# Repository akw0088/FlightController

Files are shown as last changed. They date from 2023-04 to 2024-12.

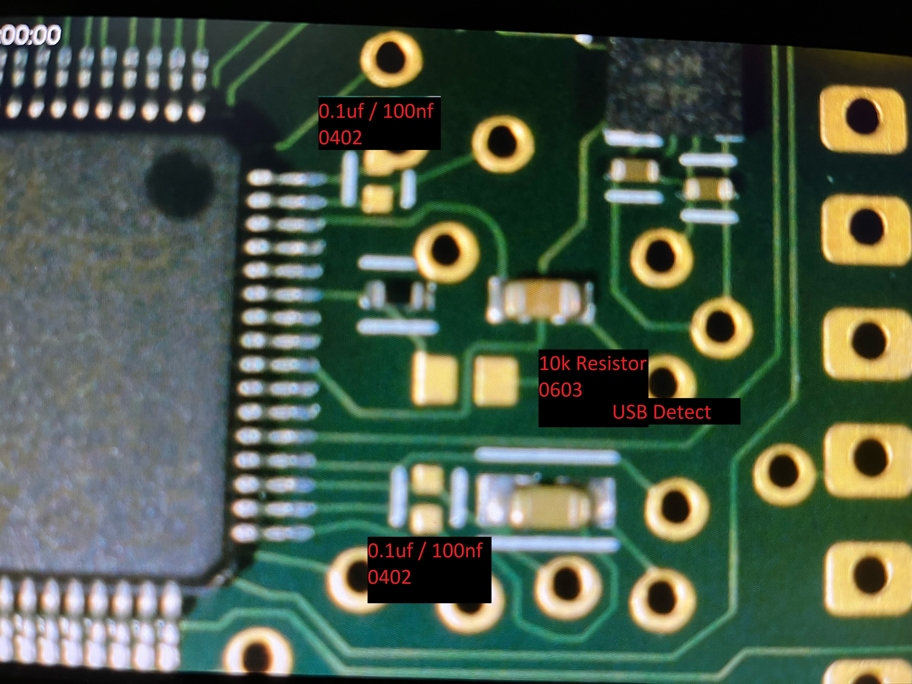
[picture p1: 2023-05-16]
boards/rev1/SMD_to_solder/image1.jpeg

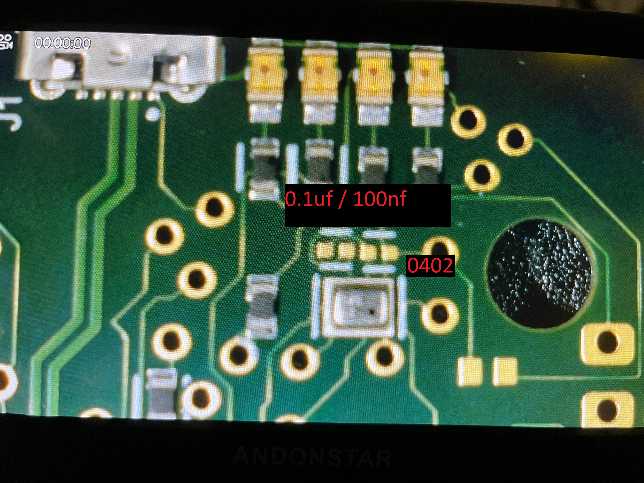
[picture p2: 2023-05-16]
boards/rev1/SMD_to_solder/image4.jpeg

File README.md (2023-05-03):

# FlightController

Figured I should design a PCB and a flight controller seemed pretty approachable compared to how complicated PC's are getting. DroneMesh designed a F4 flight controller that uses essentially three chips. The Gyro MPU6000, the processor STM32F4xx, and one diode to feed the 3.3v regulator from USB or external 5v. I would like to make a F7 flight controller and would like for it to be similar to the JBF7_V2. I am currently using Altium Designer for schematic and layout (get a free license due to my masters degreee) but I will likely make the files available in as many formats as I possibly can (KiCad, Cadence, EasyEDA, DipTrace, others?)

For the most part the schematic is the most useful, as I find this is really an exercise in picking chips and connecting nets together, layout can be automated quite a bit, but I'm sure manual part placement will occur as well as setting the 30x30 size and 4mm mounting holes.

		"Special Pins" have timers, like motor outputs, camera control, LED_STRIP, etc

For manufacturing I'll probably use PCBWay or JLCPCB

Good video/channel on PCB design:

https://www.youtube.com/watch?v=aVUqaB0IMh4

Altium specific video (cross probing two windows is awesome):

https://www.youtube.com/watch?v=PMEpQZ90f34

Links to drone meshes stuff:

https://oshwlab.com/mesh.drone/mesh-fc-v1-backup

https://www.pcbway.com/project/member/?bmbno=82F43017-E23A-4A

https://www.youtube.com/c/DroneMesh

Drone mesh PCB with OSD chip (not sure he ever got it working):

https://easyeda.com/modules/DroneMesh-OpenFC-Schematic_02d7d85512334af9a66e7b7c09a951f3

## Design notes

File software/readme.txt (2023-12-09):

Above is mostly auto generated from STM32CubeIDE

	Bootloader boot works
	Software runs when programming from bootloader
	Clocking issue resolved USB in non-bootloader mode
	(8mhz external clock HSE, was set to 27mhz originally as that was what was originally in the BOM, but what was built on the PCB was actually 8mhz, which is good, because the max clock I see on the CubeIDE is 26mhz)
	USB currently comes up as STMicroelectronics Virtual COM Port (COM3)
	Need to add some software to support updating when in non-bootloader mode
	(maybe serial command to enter DFU mode?)
	Idea was to just use BetaFlight unmodified, but I'm assuming clocking differences are preventing the USB from coming up

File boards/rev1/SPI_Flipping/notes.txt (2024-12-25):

In the rev1 boards I got MOSI/MISO pins backwards to the Gyro and the Barometer (mainly because they renamed them SDI/SDO for political correctness)

So, to fix them I used a NF.V2 Grinding Pen to cut the traces
(probably overkill, as I could have probably just used a snap away razor knife to cut the traces, eg: https://www.youtube.com/watch?v=ozH2F3AX8BY)

I suppose the grinding pen can get middle layer traces also if you are delicate

Anyway, looking at the small size of these traces I think soldering to them would be pretty difficult, so I think between copper tape and conductive ink pen I can connect them more easily. Although the pen is kind of pricey at $60 and has a short shelf life of 18 months. (Bought this one: CW2200MTP)

In summary: I ordered five rev1 boards, two have SMD component soldered up and work. (Not all components were pick and placed) Board one I shorted the voltage regulator, but can still be used for testing the Analog video OCD chip I believe. The next two boards had the SMD components soldered and work, and that leaves two untouched boards.

Probably would have been faster to just order more boards with the trace fixed in software and worked with JLCPCB to get all the SMD components connected from factory. But I want Rev2 to be perfect or near perfect so the more I can test on rev1 the better.

(That said I made rev1 in about a week while taking time off work when I had a wisdom tooth removed and probably should have reviewed the schematic more intensely prior to getting it made)

12/24/2024

Added solder pen to the board for the SPI flip on the gyro only for now. Passes basic conductivity checks with a multimeter. Got really close to the vias but I lucked out, almost seems like a slight edge there preventing accidental bridging which is nice

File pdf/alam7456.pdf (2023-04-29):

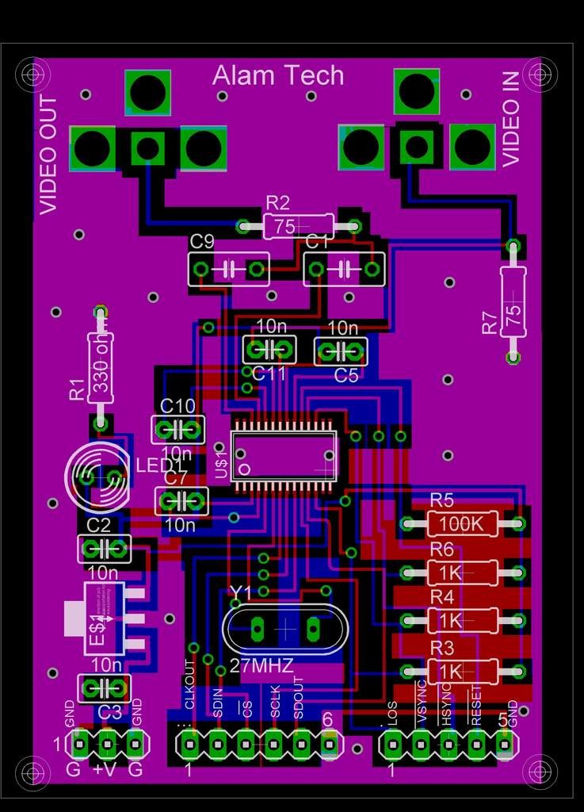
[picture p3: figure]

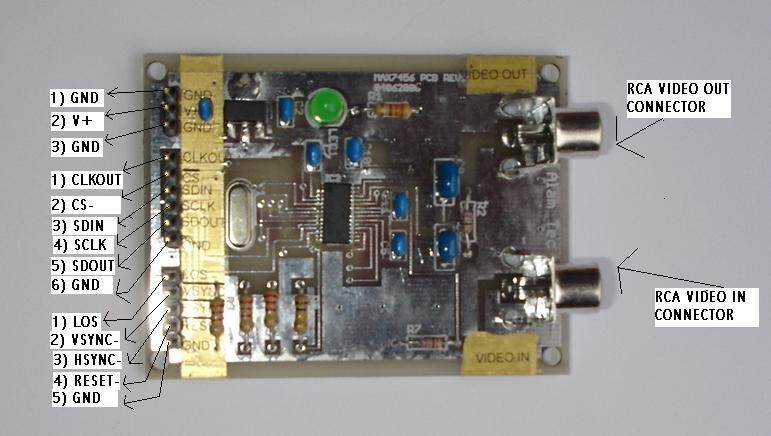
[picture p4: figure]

MAX7456 DEV BOARD WITH ALL SIGNALS INFO

### MAX7456 ON SCREEN DISPLAY DEVLOPMENT BOARD

General Description:
The MAX7456 Development Board is a fully assembled and tested Printed-Circuit Board (PCB) that supports SPI interface to MAX7456 signal-channel monochrome on-screen display (OSD) with integrated video driver.

The MAX7456 is single channel monochrome on-screen display(OSD) generator lowers the system cost by eliminating the need for an external video driver, sync separator, video switch and EEPROM. The MAX7456 serves all market with 256 user programmable characters in NTSC and PAL Standards.

The MAX7456 can easily display information such as
1. Company logo.
2. Custom graphics.
3. Time.
4. Date.
5. Arbitrary character size.

The MAX7456 is preloaded with 256 characters and pictograph and can be reprogrammed in-circuit using SPI port.

The MAX7456 is available in a 28 pin TSSOP package and is fully specified over the extended (-40 degree C to +85 degree C) temperature range.

The power LED shows the +5V on board.
Total current MAX7456 board consumes is around 100 ma, power consumption is around 0.5W.

Application:
Security Switching Systems.
Security Cameras.
Industrial Application.
In-Cabin Entertainment.
Consumer Electronics.

Recommended Equipment:
VCC accepts 7-12 Volt 250ma power supply. NTSC or PAL signal source.
NTSC or PAL video monitor.
Video Cable (RCA cable not included).

Do not turn on the power until all connections are made.

Features:
256 User-Defined Character or Pictograph in integrated EEPROM. 12X18 Pixel Character Size.
Blinking, Inverse and Background Control Character Attribute. Selectable Brightness by Row.
Display up to 16 Row and 30 Characters.
Sag Compensation on Video-Driver Outputs.
LOS, VSYNC(active low), HSYNC(active low) and clock output. Integral Sync Generation.
NTSC and PAL Compatible.
SPI-Compatible Serial Interface.
Delivered With Preprogrammed Character Set.

MAX7456 Dev Board Signals:
1. LOS: LOS goes high when 32 consecutive valid sync pulses are missing. Connect to 1k or 2.2 k pull up resistor to DVDD or another positive supply voltage suitable for the receiving device. If user want different pull up he can cut the pull up resistor and user external ones.
2. VSYNC: Vertical Sync Output (Open Drain, active low). VSYNC goes low following the video input vertical sync internal. VSYNC is either recovered from VIN or internally generated when internal sync mode used. Connect to 1k or 2.2 k pull up resistor to DVDD or another positive supply voltage suitable for the receiving device. If user want different pull up he can cut the pull up resistor and user external ones.
3. HSYNC: Horizontal Sync Output (Open Drain, active low). HSYNC goes low following the video input horizontal sync interval.
4. RESET: System Reset Input. The minimum RESET Pulse width is 50 msec. All SPI register are reset to their default values after 100 usec following rising edge of RESET. The display memory is reset to its default value of 00h in all location after 20usec following the rising edge of RESET.
5. VIDEO IPUT: The MAX7456 accepts NTSC or PAL CVBS Signals at VIN. The video signal input must be AC-Coupled with a 0.1uf capacitor and internally coupled. An input coupling capacitance of 0.1uf is required to guarantee the specific line-time distortion (LTD) and video clamp setting time.
6. Sync Separator: The sync separator detects the composite sync pulses on the Video Input and extracts the timing information to generate HSYNC and VSYNC. LOS goes high if no sync signal is detected at VIN for 32 consecutive lines and goes low if 32 consecutive horizontal sync signals are detected.
7. Serial Interface: The SPI compatible Serial Interface programs the operating mode and OSD data Read capability permits Write verification and reading the status (STAT), Display Memory Data Out (DMDO) and Character Memory Data Out(CMDO) registers.
8. Video-Driver Output: The MAX7456 includes a Video-driver output with a gain of 2. The driver has a maximum of 2.4Vp-p output swing and a 6MHZ large signal bandwidth. The driver is capable of driving two 150ohms standard video loads.

For MAX7456 data sheet, please check these links, you will find sample code along with other useful information.

http://www.maxim-ic.com/
http://www.rcgroups.com/forums/showthread.php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

Here is the video at youtube.
http://www.youtube.com/watch?v=RTPLH7UWspw

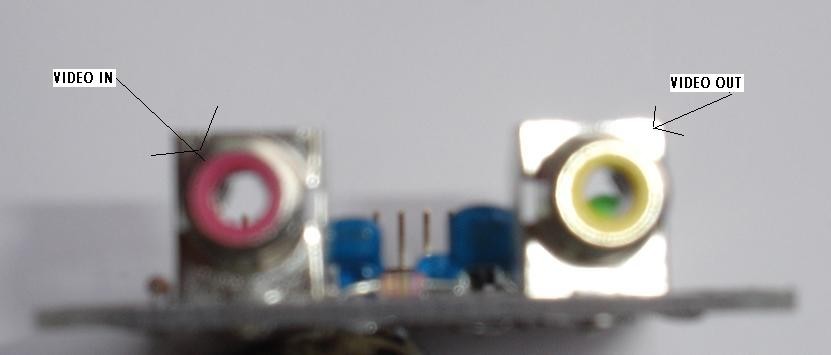
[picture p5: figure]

MAX7456 DEV BOARD VIDEO IN-OUT RCA CONNECTOR

MAX7456 DEV BOARD COMPLETE LAYOUT

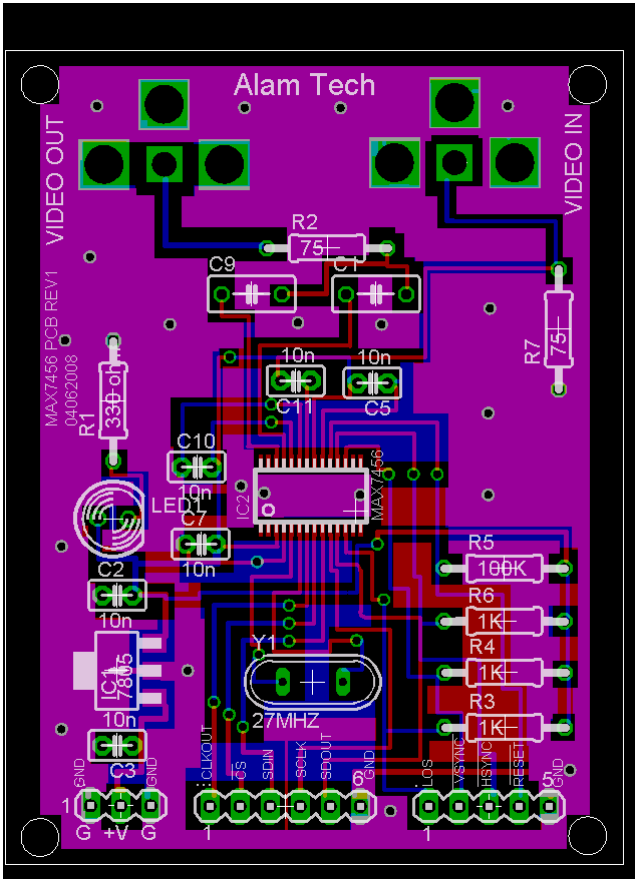
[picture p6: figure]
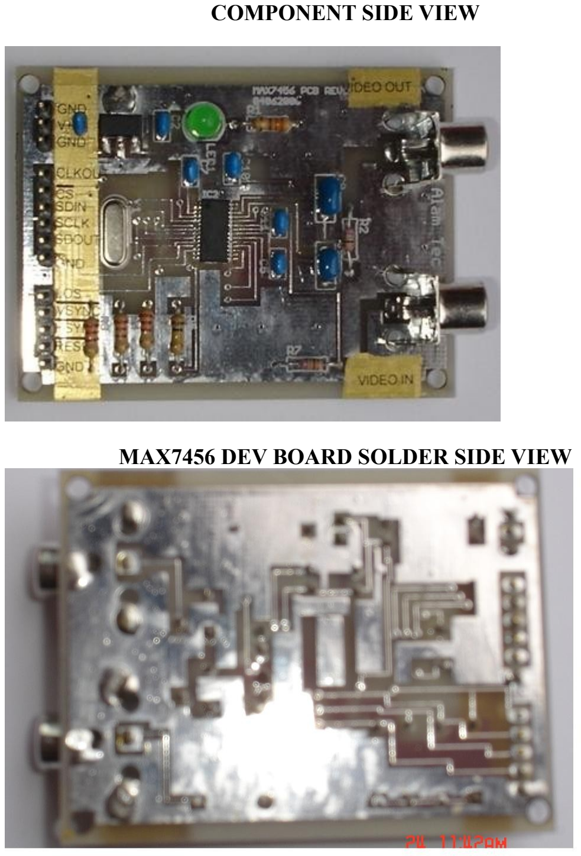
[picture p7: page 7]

COMPONENT SIDE VIEW

MAX7456 DEV BOARD SOLDER SIDE VIEW

Here is the function, I just wrote it for testing your sequence.

void show_misc_data_display (void)
{
/* ENABLE VIDEO OUTPUT */
max7456_add_reg = MAX7456_VIDEO_0_REG_ADD; max7456_data_reg = ENABLE_DISPLAY_OSD_IMAGE; spi_enable_cs_new();
/* send 8 bit address */
spi_send_data_to_spi_port(max7456_add_reg);
/* send 8 bit data */
spi_send_data_to_spi_port(max7456_data_reg); spi_disable_cs();

/* SEND ADDRESS */
max7456_add_reg = MAX7456_DISPLAY_MEMORY_ADDRESS_HIGH; max7456_data_reg = 0x00;
spi_enable_cs_new();
/* send 8 bit address */
spi_send_data_to_spi_port(max7456_add_reg); /* send 8 bit data */
spi_send_data_to_spi_port(max7456_data_reg); spi_disable_cs();
max7456_add_reg = MAX7456_DISPLAY_MEMORY_ADDRESS_LOW; max7456_data_reg = 0xE0;
spi_enable_cs_new();
/* send 8 bit address */
spi_send_data_to_spi_port(max7456_add_reg); /* send 8 bit data */
spi_send_data_to_spi_port(max7456_data_reg); spi_disable_cs();
/* SEND DATA */
max7456_add_reg = MAX7456_DISPLAY_DATA_IN; max7456_data_reg = 0x0B;
spi_enable_cs_new();
spi_send_data_to_spi_port(max7456_add_reg); spi_send_data_to_spi_port(max7456_data_reg); spi_disable_cs();

/* SEND ADDRESS */
max7456_add_reg = MAX7456_DISPLAY_MEMORY_ADDRESS_HIGH; max7456_data_reg = 0x00;
spi_enable_cs_new();
/* send 8 bit address */
spi_send_data_to_spi_port(max7456_add_reg); /* send 8 bit data */
spi_send_data_to_spi_port(max7456_data_reg); spi_disable_cs();
max7456_add_reg = MAX7456_DISPLAY_MEMORY_ADDRESS_LOW; max7456_data_reg = 0xE1;
spi_enable_cs_new();
spi_send_data_to_spi_port(max7456_add_reg); spi_send_data_to_spi_port(max7456_data_reg);

spi_disable_cs();
/* SEND DATA */
max7456_add_reg = MAX7456_DISPLAY_DATA_IN; max7456_data_reg = 0x0C;
spi_enable_cs_new();
spi_send_data_to_spi_port(max7456_add_reg); spi_send_data_to_spi_port(max7456_data_reg); spi_disable_cs();

/* SEND ADDRESS */
max7456_add_reg = MAX7456_DISPLAY_MEMORY_ADDRESS_HIGH; max7456_data_reg = 0x00;
spi_enable_cs_new();
spi_send_data_to_spi_port(max7456_add_reg); spi_send_data_to_spi_port(max7456_data_reg); spi_disable_cs();
max7456_add_reg = MAX7456_DISPLAY_MEMORY_ADDRESS_LOW; max7456_data_reg = 0xE2;
spi_enable_cs_new();
spi_send_data_to_spi_port(max7456_add_reg); spi_send_data_to_spi_port(max7456_data_reg); spi_disable_cs();
/* SEND DATA */
max7456_add_reg = MAX7456_DISPLAY_DATA_IN; max7456_data_reg = 0x0D;
spi_enable_cs_new();
spi_send_data_to_spi_port(max7456_add_reg); spi_send_data_to_spi_port(max7456_data_reg); spi_disable_cs();
}

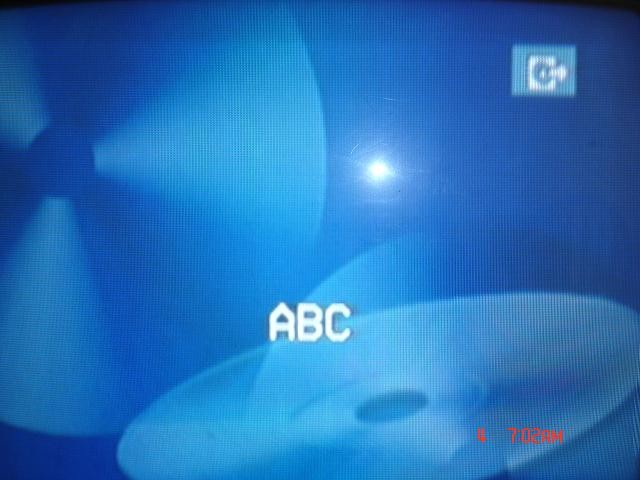
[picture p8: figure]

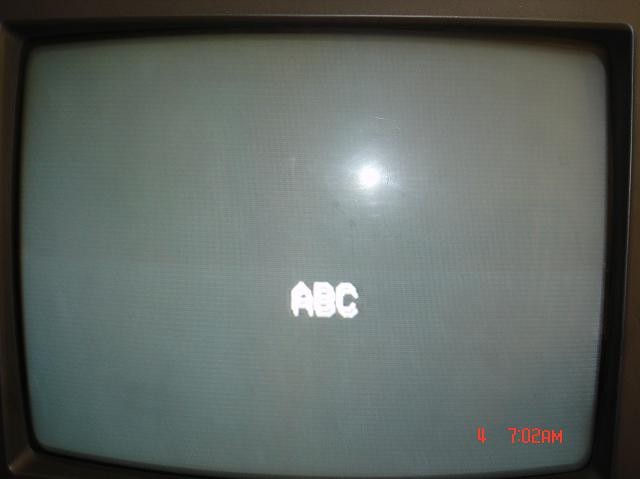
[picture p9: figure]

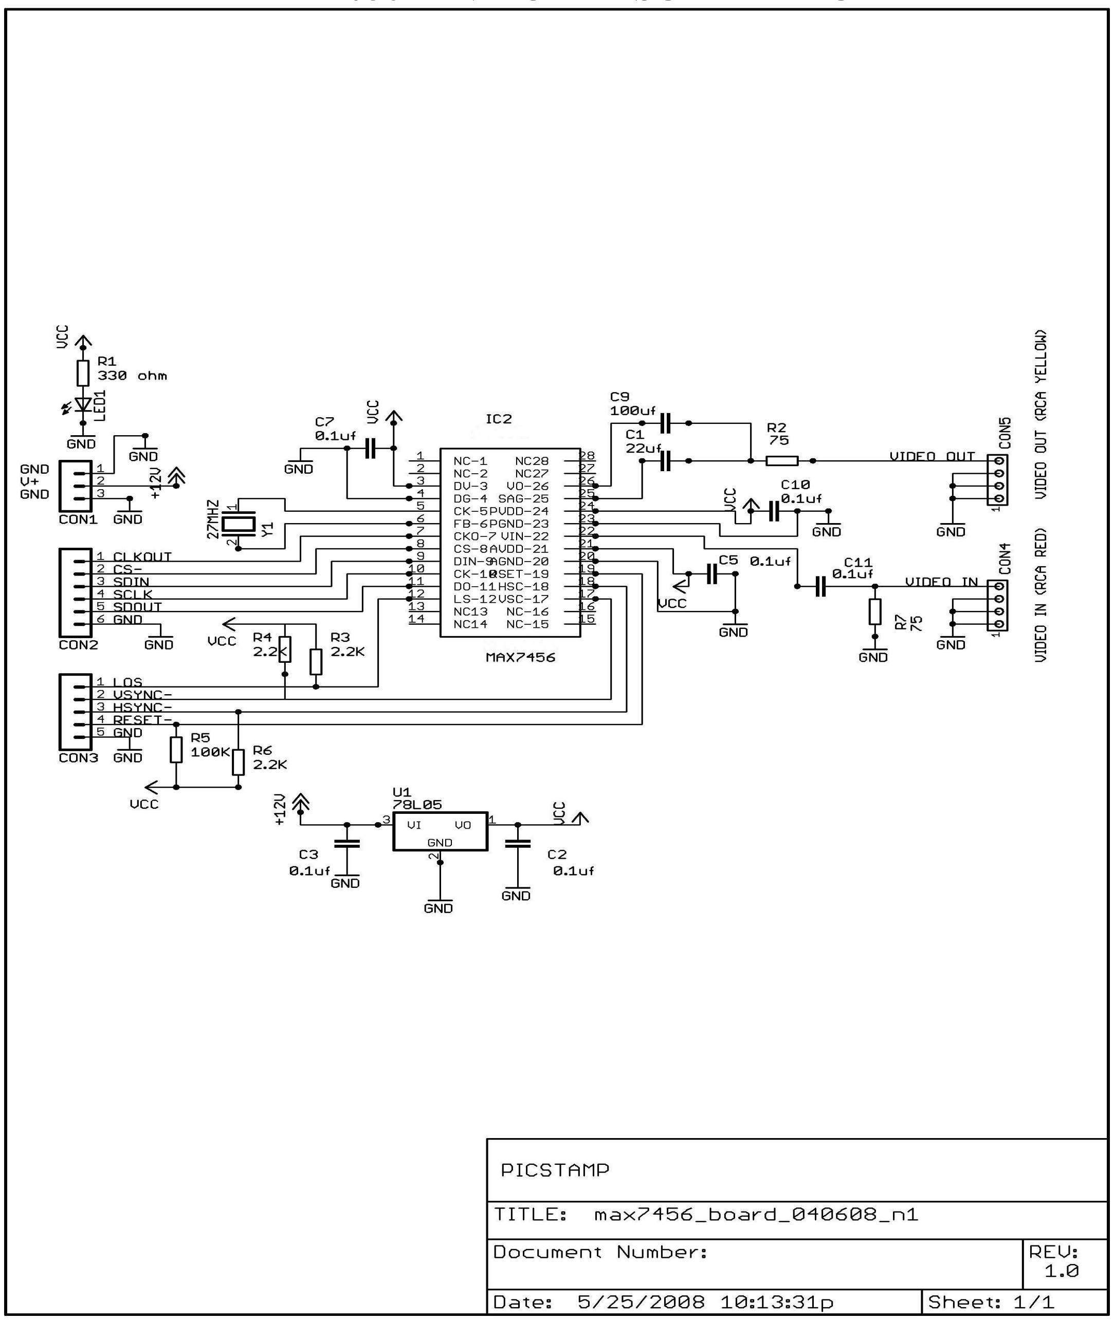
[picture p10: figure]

MAX756 DEV BOARD SCHEMATIC

MAX7456 Board Specification:
1. Board width is 2.0625 inches.
2. Board length is 2.625 inches.
3. Board weight is 0.6250 oz (20 grams).

MAX7456 Board using with +5v supply:

Please short the pin 1 with pin 3 of U1 (7805) voltage regulator.
Check the picture below, just short the pin1 and pin3, so by doing this voltage regulator can be bypass.
Please disconnect R3, R4, R5, R6 if you want to connect the LOS, RESET, VSYNC, HSYNC to 3.3 volt device, use external pull up resistors. All these signals are pull up using +5 volt.

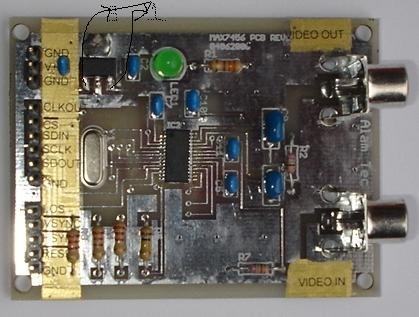
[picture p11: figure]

MAX756 DEV BOARD CONNETORS:

CON1: (MAIN POWER IN)
INTERFACE | PIN
GND | 1
VCC (+7 to +15V) | 2
GND | 3

CON2: (SPI INTERFACE)
INTERFACE | PIN
CLKOUT (MAX7456 CLK OUT) | 1
CS- (SPI) | 2
SDIN (SPI) | 3
SCLK (SPI) | 4
SDOUT (SPI) | 5
GND | 6

CON3: (MAX7456 STATUS OUT)
INTERFACE | PIN
LOS (ACTIVE HIGH) | 1
VSYNC - (ACTIVE LOW) | 2
HSYNC - (ACTIVE LOW) | 3
RESET- (ACTIVE LOW) | 4
GND | 5

CON4: (RCA VIDEO IN CONNECTOR)
INTERFACE | PIN
GND | 1
GND | 2
GND | 3
VIDEO IN (NTSC/PAL) | 4

CON5: (RCA VIDEO OUT CONNECTOR)
INTERFACE | PIN
GND | 1
GND | 2
GND | 3
VIDEO OUT (NTSC/PAL) | 4

MAX756 Dev Board Part List:

PARTS | SPECS | MECH SPEC
CON1 | 3 PIN (POWER) | 0.1 INCH SPACING
CON2 | 6 PIN (SPI) | 0.1 INCH SPACING
CON3 | 5 PIN (SIGNALS) | 0.1 INCH SPACING
CON4 | 4 PIN (VIDEO IN) | RCA CONNECTOR
CON5 | 4 PIN (VIDEIO OUT) | RCA CONNECTOR
R1 | 330 OHMS | ¼ W
LED1 | GREEN LED
Y1 | 27 MHZ
C7 | 0.1 UF | 50 V
R4 | 2.2 K | ¼ W
R3 | 2.2 K | ¼ W
R5 | 100 K | ¼ W
R6 | 2.2 K | ¼ W
U1 | 78L05 | 500 ma +5v regulator
C9 | 100 UF | 16 V
C1 | 22 UF | 16 V
R2 | 75 OHMS | ¼ W
C10 | 0.1UF | 50 V
C5 | 0.1UF | 50 V
C11 | 0.1UF | 50V
R7 | 75 OHMS
IC2 | MAX7456 | 28 PIN TSSOP
C3 | 0.1UF | 50 V
C2 | 0.1UF | 50V

For more information please contact.

Fakhre Alam
AlamTech
4985 West 7th St, #10
Reno, Nevada, 89503
U.S.A.
fakhre@rocketmail.com

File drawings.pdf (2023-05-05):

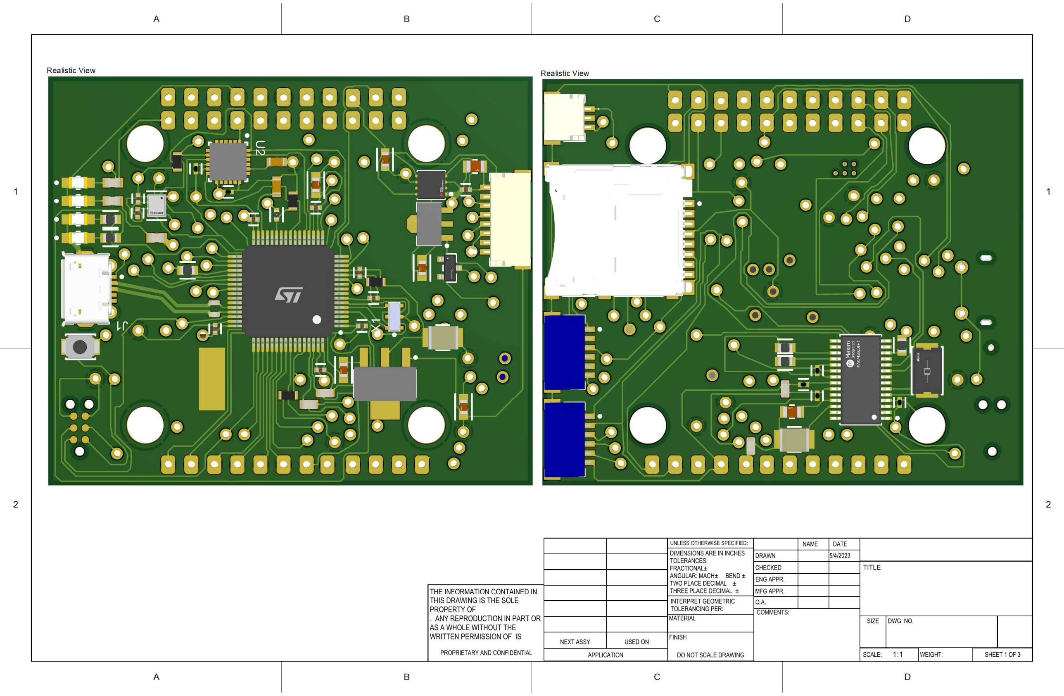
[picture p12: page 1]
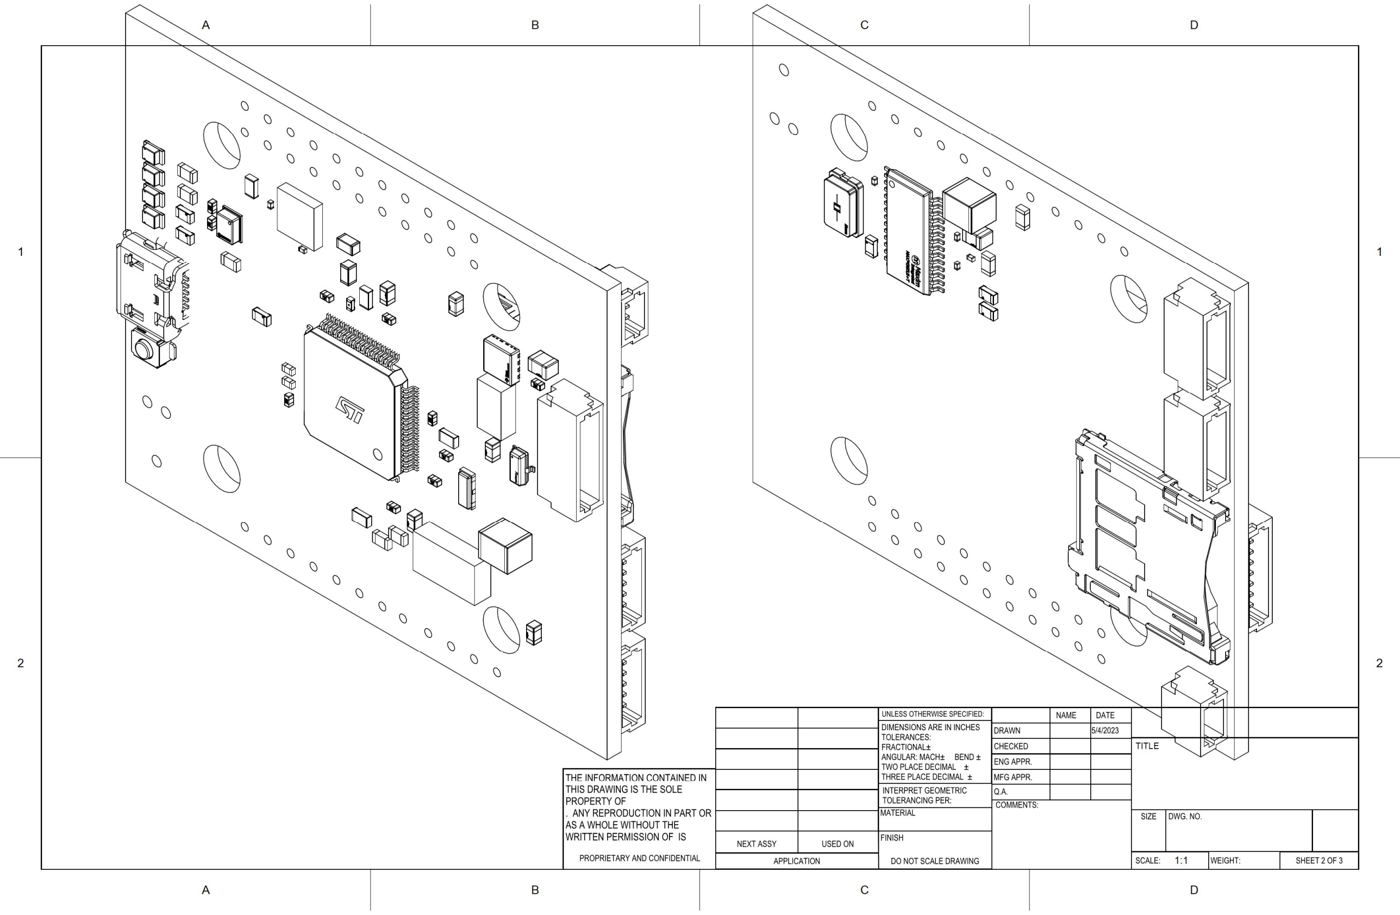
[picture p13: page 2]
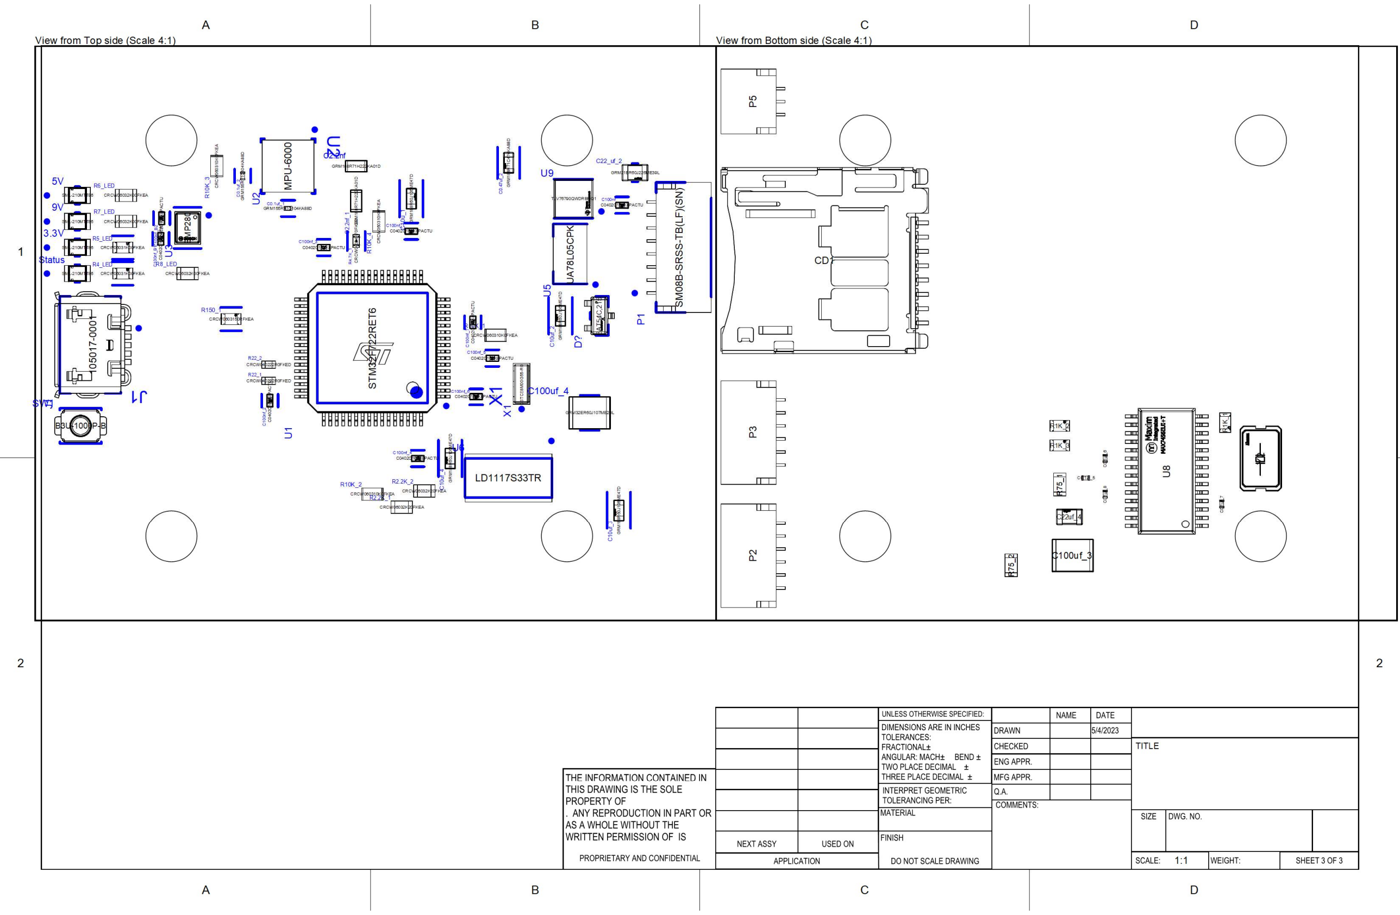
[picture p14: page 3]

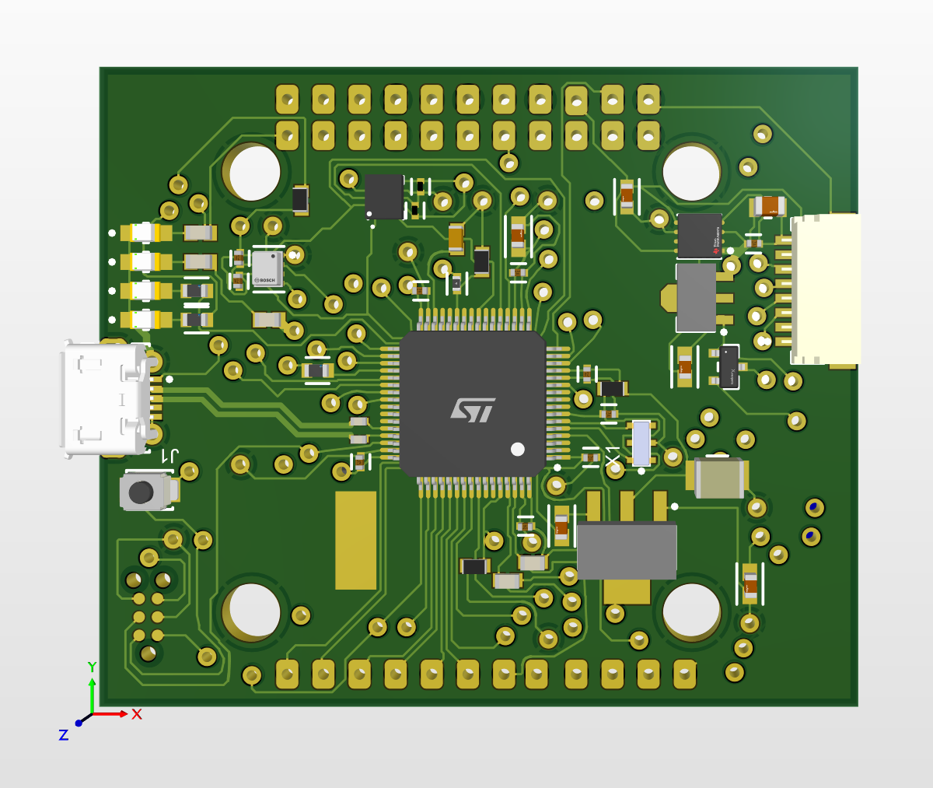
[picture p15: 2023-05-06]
top.png

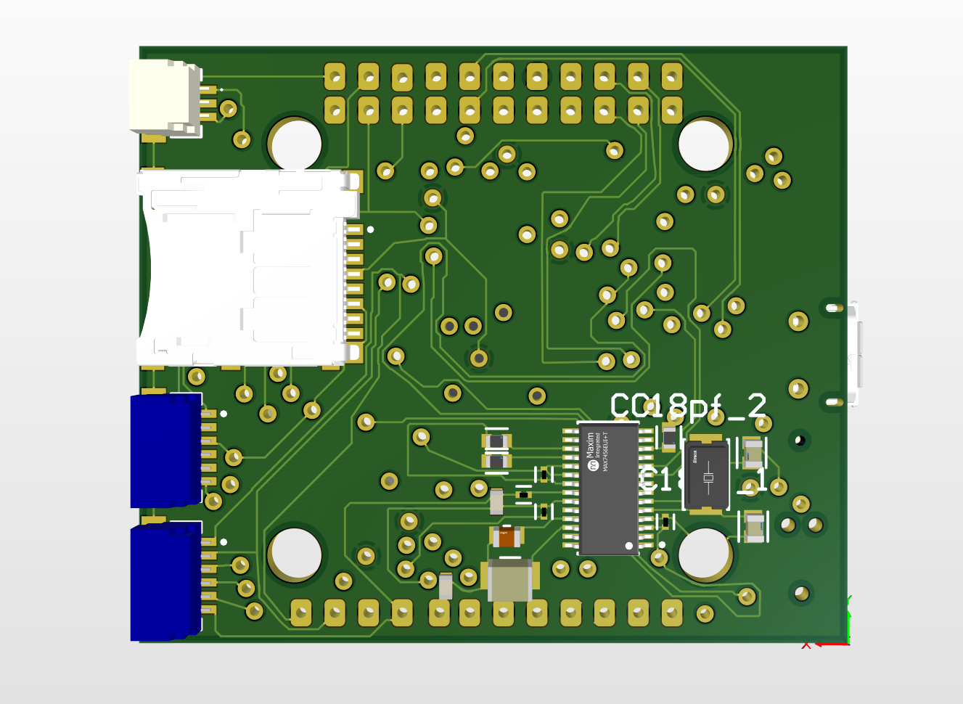
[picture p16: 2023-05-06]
bottom.png

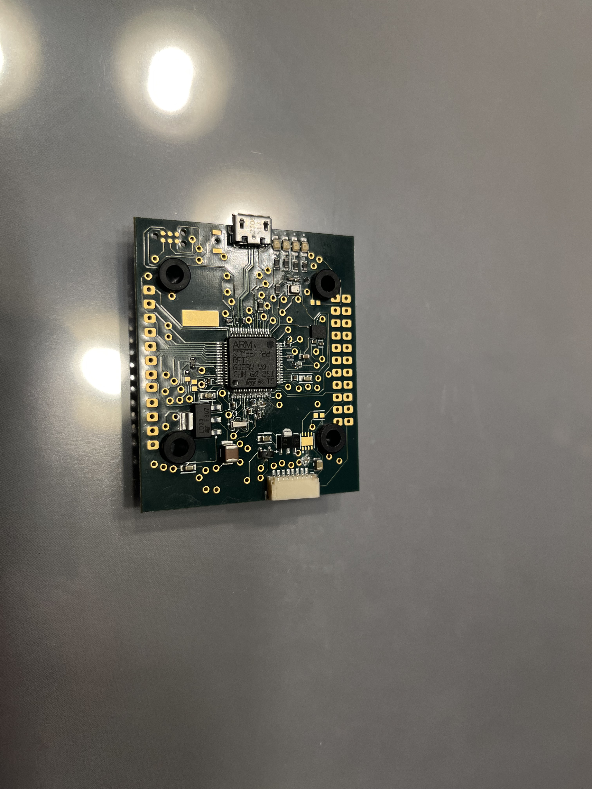
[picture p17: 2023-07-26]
boards/rev1/mounting_hole_spacing_with_grommets/Mount3.jpg

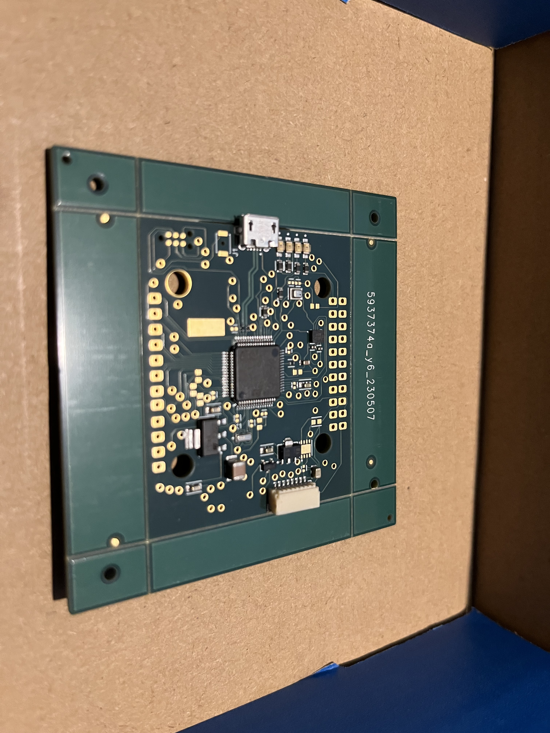
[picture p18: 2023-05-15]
boards/rev1/rev1_top.jpg

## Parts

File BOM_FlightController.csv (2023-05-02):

Line # | Name | Description | Designator | Revision ID | Revision Status | Manufacturer 1 | Manufacturer Part Number 1 | Manufacturer Lifecycle 1 | Supplier 1 | Supplier Part Number 1 | Supplier Unit Price 1 | Supplier Subtotal 1
 | Capacitor 4.7µF +/-40% 25V 0805 | Chip Capacitor, 4.7µF +/-40%, 25V, 0805, Thickness 1.45 mm |  | CMP-001-00080-4 | Up to date | Kyocera AVX | 08053D475MAT2A | Volume Production | Mouser | 581-08053D475MAT2A | 0 | 0
 | Capacitor 100 nF +/-10% 50 V 0805 | Chip Capacitor, 100 nF, +/- 10%, 50 V, 0805 (2012 Metric) |  | CMP-001-00018-6 | Up to date | Yageo | CC0805KRX7R9BB104 | Volume Production | Digi-Key | 311-1140-1-ND | 0 | 0
 | Capacitor 100 nF +/-10% 50 V 0805 | Chip Capacitor, 100 nF, +/- 10%, 50 V, 0805 (2012 Metric) |  | CMP-001-00018-6 | Up to date | Yageo | CC0805KRX7R9BB104 | Volume Production | Digi-Key | 311-1140-1-ND | 0 | 0
 | Capacitor 100 nF +/-10% 50 V 0805 | Chip Capacitor, 100 nF, +/- 10%, 50 V, 0805 (2012 Metric) |  | CMP-001-00018-6 | Up to date | Yageo | CC0805KRX7R9BB104 | Volume Production | Digi-Key | 311-1140-1-ND | 0 | 0
 | Resistor 100k +/-1% 0805 125 mW | Chip Resistor, 100 KOhm, +/- 1%, 0.125 W, -55 to 155 degC, 0805 (2012 Metric) |  | CMP-009-00024-5 | Up to date | Yageo | RC0805FR-07100KL | Volume Production | Digi-Key | 311-100KCRCT-ND | 0 | 0
 | SML-210MTT86 | LED GREEN CLEAR 0805 SMD | 3.3V | CMP-08952-000013-1 | Up to date | Rohm | SML-210MTT86 | Not Recommended for New Design | Future Electronics | 9239369 | 0.34 | 1.36
 | SML-210MTT86 | LED GREEN CLEAR 0805 SMD | 5V | CMP-08952-000013-1 | Up to date | Rohm | SML-210MTT86 | Not Recommended for New Design | Future Electronics | 9239369 | 0.34 | 1.36
 | SML-210MTT86 | LED GREEN CLEAR 0805 SMD | 9V | CMP-08952-000013-1 | Up to date | Rohm | SML-210MTT86 | Not Recommended for New Design | Future Electronics | 9239369 | 0.34 | 1.36
 | GRM155R71C104KA88D | CAP CER 0.1UF 16V X7R 0402 | C0.1uf_1 | CMP-2100-03641-2 | Up to date | Murata | GRM155R71C104KA88D | Not Recommended for New Design | Mouser | 81-GRM155R71C104KA88 | 0.017 | 0.17
 | GRM155R71C104KA88D | CAP CER 0.1UF 16V X7R 0402 | C0.1uf_2 | CMP-2100-03641-2 | Up to date | Murata | GRM155R71C104KA88D | Not Recommended for New Design | Mouser | 81-GRM155R71C104KA88 | 0.017 | 0.17
 | GRM155R71C104KA88D | CAP CER 0.1UF 16V X7R 0402 | C0.1uf_5 | CMP-2100-03641-2 | Up to date | Murata | GRM155R71C104KA88D | Not Recommended for New Design | Mouser | 81-GRM155R71C104KA88 | 0.017 | 0.17
 | GRM155R71C104KA88D | CAP CER 0.1UF 16V X7R 0402 | C0.1uf_6 | CMP-2100-03641-2 | Up to date | Murata | GRM155R71C104KA88D | Not Recommended for New Design | Mouser | 81-GRM155R71C104KA88 | 0.017 | 0.17
 | GRM155R71C104KA88D | CAP CER 0.1UF 16V X7R 0402 | C0.1uf_7 | CMP-2100-03641-2 | Up to date | Murata | GRM155R71C104KA88D | Not Recommended for New Design | Mouser | 81-GRM155R71C104KA88 | 0.017 | 0.17
 | GRM155R71C104KA88D | CAP CER 0.1UF 16V X7R 0402 | C0.1uf_8 | CMP-2100-03641-2 | Up to date | Murata | GRM155R71C104KA88D | Not Recommended for New Design | Mouser | 81-GRM155R71C104KA88 | 0.017 | 0.17
 | GRM188R71C474KA88D | Chip Multilayer Ceramic Capacitors for General Purpose, 0603, 0.47uF, X7R, 15%, 10%, 16V | C0.47uf_1 | CMP-2006-02860-2 | Up to date | Murata | GRM188R71C474KA88D | Volume Production | Newark | 03AC2674 | 0.021 | 0.042
 | GRM188R71C474KA88D | Chip Multilayer Ceramic Capacitors for General Purpose, 0603, 0.47uF, X7R, 15%, 10%, 16V | C0.47uf_2 | CMP-2006-02860-2 | Up to date | Murata | GRM188R71C474KA88D | Volume Production | Newark | 03AC2674 | 0.021 | 0.042
 | GRM155R61A105KE15D | CAP CER 1UF 10V X5R 0402 | C1u_1 | CMP-2008-04556-2 | Up to date | Murata | GRM155R61A105KE15D | Obsolete | Arrow Electronics | GRM155R61A105KE15D | 0.0046 | 46
 | GRM155R61A105KE15D | CAP CER 1UF 10V X5R 0402 | C1u_2 | CMP-2008-04556-2 | Up to date | Murata | GRM155R61A105KE15D | Obsolete | Arrow Electronics | GRM155R61A105KE15D | 0.0046 | 46
 | GRM188R71H222KA01D | Chip Capacitor, 2.2 nF, +/- 10%, 50 V, -55 to 125 degC, 0603 (1608 Metric), RoHS, Tape and Reel | C2.2nf | CMP-2006-02908-5 | Up to date | Murata | GRM188R71H222KA01D | Obsolete | Arrow Electronics | GRM188R71H222KA01D | 0.0139 | 55.6
 | GRM188R71H222KA01D | Chip Capacitor, 2.2 nF, +/- 10%, 50 V, -55 to 125 degC, 0603 (1608 Metric), RoHS, Tape and Reel | C2.2nf_1 | CMP-2006-02908-5 | Up to date | Murata | GRM188R71H222KA01D | Obsolete | Arrow Electronics | GRM188R71H222KA01D | 0.0139 | 55.6
 | GRM188R71H103KA01D | Chip Capacitor, 10 nF, +/- 10%, 50 V, -55 to 125 degC, 0603 (1608 Metric), RoHS, Tape and Reel | C10n_1 | CMP-2100-03642-1 | Up to date | Murata | GRM188R71H103KA01D | Obsolete | Arrow Electronics | GRM188R71H103KA01D | 0.0042 | 16.8
 | GRM188R60J106ME47D | Chip Multilayer Ceramic Capacitors for General Purpose, 0603, 10uF, X5R, 15%, 20%, 6.3V | C10u_1 | CMP-2006-02792-2 | Up to date | Murata | GRM188R60J106ME47D | Volume Production | Newark | 03AC2652 | 0.029 | 0.116
 | GRM188R60J106ME47D | Chip Multilayer Ceramic Capacitors for General Purpose, 0603, 10uF, X5R, 15%, 20%, 6.3V | C10uf_2 | CMP-2006-02792-2 | Up to date | Murata | GRM188R60J106ME47D | Volume Production | Newark | 03AC2652 | 0.029 | 0.116
 | GRM188R60J106ME47D | Chip Multilayer Ceramic Capacitors for General Purpose, 0603, 10uF, X5R, 15%, 20%, 6.3V | C10uf_3 | CMP-2006-02792-2 | Up to date | Murata | GRM188R60J106ME47D | Volume Production | Newark | 03AC2652 | 0.029 | 0.116
 | GRM188R60J106ME47D | Chip Multilayer Ceramic Capacitors for General Purpose, 0603, 10uF, X5R, 15%, 20%, 6.3V | C10uf_4 | CMP-2006-02792-2 | Up to date | Murata | GRM188R60J106ME47D | Volume Production | Newark | 03AC2652 | 0.029 | 0.116
 | GRM21BR60J226ME39L | Chip Multilayer Ceramic Capacitors for General Purpose, 0805, 22uF, X5R, 15%, 20%, 6.3V | C22_uf | CMP-2007-03385-2 | Up to date | Murata | GRM21BR60J226ME39L | Volume Production | Newark | 24R6338 | 0.077 | 0.231
 | GRM21BR60J226ME39L | Chip Multilayer Ceramic Capacitors for General Purpose, 0805, 22uF, X5R, 15%, 20%, 6.3V | C22_uf_2 | CMP-2007-03385-2 | Up to date | Murata | GRM21BR60J226ME39L | Volume Production | Newark | 24R6338 | 0.077 | 0.231
 | GRM21BR60J226ME39L | Chip Multilayer Ceramic Capacitors for General Purpose, 0805, 22uF, X5R, 15%, 20%, 6.3V | C22uf_4 | CMP-2007-03385-2 | Up to date | Murata | GRM21BR60J226ME39L | Volume Production | Newark | 24R6338 | 0.077 | 0.231
 | C0402C104K8PACTU | CAP CER 0.1UF 10V X5R 0402 | C100nf | CMP-2008-02046-2 | Up to date | KEMET | C0402C104K8PACTU | Volume Production | Newark | 49H5566 | 0.005 | 0.04
 | C0402C104K8PACTU | CAP CER 0.1UF 10V X5R 0402 | C100nf_1 | CMP-2008-02046-2 | Up to date | KEMET | C0402C104K8PACTU | Volume Production | Newark | 49H5566 | 0.005 | 0.04
 | C0402C104K8PACTU | CAP CER 0.1UF 10V X5R 0402 | C100nf_2 | CMP-2008-02046-2 | Up to date | KEMET | C0402C104K8PACTU | Volume Production | Newark | 49H5566 | 0.005 | 0.04
 | C0402C104K8PACTU | CAP CER 0.1UF 10V X5R 0402 | C100nf_3 | CMP-2008-02046-2 | Up to date | KEMET | C0402C104K8PACTU | Volume Production | Newark | 49H5566 | 0.005 | 0.04
 | C0402C104K8PACTU | CAP CER 0.1UF 10V X5R 0402 | C100nf_4 | CMP-2008-02046-2 | Up to date | KEMET | C0402C104K8PACTU | Volume Production | Newark | 49H5566 | 0.005 | 0.04
 | C0402C104K8PACTU | CAP CER 0.1UF 10V X5R 0402 | C100nf_5 | CMP-2008-02046-2 | Up to date | KEMET | C0402C104K8PACTU | Volume Production | Newark | 49H5566 | 0.005 | 0.04
 | C0402C104K8PACTU | CAP CER 0.1UF 10V X5R 0402 | C100nf_B1 | CMP-2008-02046-2 | Up to date | KEMET | C0402C104K8PACTU | Volume Production | Newark | 49H5566 | 0.005 | 0.04
 | C0402C104K8PACTU | CAP CER 0.1UF 10V X5R 0402 | C100nf_B2 | CMP-2008-02046-2 | Up to date | KEMET | C0402C104K8PACTU | Volume Production | Newark | 49H5566 | 0.005 | 0.04
 | GRM32ER60J107ME20L | CAP CER 100UF 6.3V X5R 1210 | C100uf_3 | CMP-2000-05259-2 | Up to date | Murata | GRM32ER60J107ME20L | Not Recommended for New Design | Future Electronics | 2114105 | 1.23 | 2.46
 | GRM32ER60J107ME20L | CAP CER 100UF 6.3V X5R 1210 | C100uf_4 | CMP-2000-05259-2 | Up to date | Murata | GRM32ER60J107ME20L | Not Recommended for New Design | Future Electronics | 2114105 | 1.23 | 2.46
 | 502774-0891 | Micro SD Memory Card Connector, 0.5 A, 10 V (DC), -25 to 85 degC, 8-Pin SMT, RoHS, Tape and Reel | CD1 | CMP-2000-05248-1 | Up to date | Molex | 5027740891 | Unknown | Newark | 67X4867 | 2.58 | 2.58
 | BAT54C | Schottky Barrier Diode, 30 V, 2 uA, -55 to 150 degC, 3-Pin SOT23, RoHS, Tape and Reel | D1 | CMP-0417-00003-1 | Up to date | NXP Semiconductors | BAT54C | Unknown
 | 105017-0001 | Micro-USB B Receptacle, Right Angle, Bottom Mount, Surface Mount, with Solder Tabs, -30 to 85 degC, 5-Pin USB, RoHS, Tape and Reel | J1 | CMP-2000-05827-1 | Up to date | Molex | 1050170001 | Volume Production | Newark | 17AC5641 | 0.235 | 0.235
 | 742792620 | SMD EMI Suppression Ferrite Bead WE-CBF, Z = 100 Ohm | L1 | CMP-0220-00188-1 | Up to date | Wurth Electronics | 742792620 | Volume Production | Newark | 24AC5665 | 0.101 | 0.101
 | SM08B-SRSS-TB(LF)(SN) | Male Header, Pitch 1 mm, 1 x 8 Position, Height 2.95 mm, -25 to 85 degC, RoHS, Tape and Reel | P1 | CMP-2000-07082-1 | Up to date | JST | SM08B-SRSS-TB(LF)(SN) | Unknown | Digi-Key | 455-1808-1-ND | 0.88 | 0.88
 | SM06B-SRSS-TB(LF)(SN) | Male Header, Pitch 1 mm, 1 x 6 Position, Height 2.95 mm, -25 to 85 degC, RoHS, Tape and Reel | P2 | CMP-2000-07080-1 | Up to date | JST | SM06B-SRSS-TB(LF)(SN) | Volume Production | Digi-Key | 455-1806-1-ND | 0.78 | 1.56
 | SM06B-SRSS-TB(LF)(SN) | Male Header, Pitch 1 mm, 1 x 6 Position, Height 2.95 mm, -25 to 85 degC, RoHS, Tape and Reel | P3 | CMP-2000-07080-1 | Up to date | JST | SM06B-SRSS-TB(LF)(SN) | Volume Production | Digi-Key | 455-1806-1-ND | 0.78 | 1.56
 | SM03B-SRSS-TB(LF)(SN) | Male Header, Pitch 1 mm, 1 x 3 Position, Height 2.9 mm, -25 to 85 degC, RoHS, Tape and Reel | P5 | CMP-2000-07077-1 | Up to date | JST | SM03B-SRSS-TB(LF)(SN) | Unknown | Newark | 33P8180 | 0.54 | 0.54
 | CRCW06031K00FKEA | RES Thick Film, 1kΩ, 1%, 0.1W, 100ppm/°C, 0603 | R1K_1 | CMP-1666-00003-5 | Up to date | Vishay Dale | CRCW06031K00FKEA | Volume Production | Newark | 52K8016 | 0.005 | 0.035
 | CRCW06031K00FKEA | RES Thick Film, 1kΩ, 1%, 0.1W, 100ppm/°C, 0603 | R1K_2 | CMP-1666-00003-5 | Up to date | Vishay Dale | CRCW06031K00FKEA | Volume Production | Newark | 52K8016 | 0.005 | 0.035
 | CRCW06031K00FKEA | RES Thick Film, 1kΩ, 1%, 0.1W, 100ppm/°C, 0603 | R1K_3 | CMP-1666-00003-5 | Up to date | Vishay Dale | CRCW06031K00FKEA | Volume Production | Newark | 52K8016 | 0.005 | 0.035
 | CRCW06032K20FKEA |  | R2.2K_1 | CMP-2000-03167-1 | Up to date | Vishay | CRCW06032K20FKEA | Volume Production | Arrow Electronics | CRCW06032K20FKEA | 0.0248 | 0.0496
 | CRCW06032K20FKEA |  | R2.2K_2 | CMP-2000-03167-1 | Up to date | Vishay | CRCW06032K20FKEA | Volume Production | Arrow Electronics | CRCW06032K20FKEA | 0.0248 | 0.0496
 | CRCW06031K00FKEA | RES Thick Film, 1kΩ, 1%, 0.1W, 100ppm/°C, 0603 | R4_LED | CMP-1666-00003-5 | Up to date | Vishay Dale | CRCW06031K00FKEA | Volume Production | Newark | 52K8016 | 0.005 | 0.035
 | CRCW04024K70FKED | RES Thick Film, 4.7kΩ, 1%, 0.063W, 100ppm/°C, 0402 | R4.7K_1 | CMP-2002-00051-3 | Up to date | Vishay Dale | CRCW04024K70FKED | Unknown
 | CRCW06031K00FKEA | RES Thick Film, 1kΩ, 1%, 0.1W, 100ppm/°C, 0603 | R5_LED | CMP-1666-00003-5 | Up to date | Vishay Dale | CRCW06031K00FKEA | Volume Production | Newark | 52K8016 | 0.005 | 0.035
 | CRCW06031K00FKEA | RES Thick Film, 1kΩ, 1%, 0.1W, 100ppm/°C, 0603 | R9_LED | CMP-1666-00003-5 | Up to date | Vishay Dale | CRCW06031K00FKEA | Volume Production | Newark | 52K8016 | 0.005 | 0.035
 | CRCW06031K00FKEA | RES Thick Film, 1kΩ, 1%, 0.1W, 100ppm/°C, 0603 | R10_LED | CMP-1666-00003-5 | Up to date | Vishay Dale | CRCW06031K00FKEA | Volume Production | Newark | 52K8016 | 0.005 | 0.035
 | CRCW060310K0FKEA | Chip Resistor, 10 KOhm, +/- 1%, 100 mW, -55 to 155 degC, 0603 (1608 Metric), RoHS, Tape and Reel | R10K_1 | CMP-1666-00005-4 | Up to date | Vishay | CRCW060310K0FKEA | Volume Production | Newark | 52K8063 | 0.005 | 0.02
 | CRCW060310K0FKEA | Chip Resistor, 10 KOhm, +/- 1%, 100 mW, -55 to 155 degC, 0603 (1608 Metric), RoHS, Tape and Reel | R10K_2 | CMP-1666-00005-4 | Up to date | Vishay | CRCW060310K0FKEA | Volume Production | Newark | 52K8063 | 0.005 | 0.02
 | CRCW060310K0FKEA | Chip Resistor, 10 KOhm, +/- 1%, 100 mW, -55 to 155 degC, 0603 (1608 Metric), RoHS, Tape and Reel | R10K_3 | CMP-1666-00005-4 | Up to date | Vishay | CRCW060310K0FKEA | Volume Production | Newark | 52K8063 | 0.005 | 0.02
 | CRCW060310K0FKEA | Chip Resistor, 10 KOhm, +/- 1%, 100 mW, -55 to 155 degC, 0603 (1608 Metric), RoHS, Tape and Reel | R10K_4 | CMP-1666-00005-4 | Up to date | Vishay | CRCW060310K0FKEA | Volume Production | Newark | 52K8063 | 0.005 | 0.02
 | CRCW040222R0FKED |  | R22_1 | CMP-2002-08382-1 | Up to date | Vishay | CRCW040222R0FKED | Volume Production | Newark | 52K6848 | 0.003 | 0.006
 | CRCW040222R0FKED |  | R22_2 | CMP-2002-08382-1 | Up to date | Vishay | CRCW040222R0FKED | Volume Production | Newark | 52K6848 | 0.003 | 0.006
 | ERJ-3EKF75R0V |  | R75_1 | CMP-2000-00639-1 | Up to date | Panasonic | ERJ-3EKF75R0V | Volume Production | Newark | 65T8518 | 0.003 | 0.006
 | ERJ-3EKF75R0V |  | R75_2 | CMP-2000-00639-1 | Up to date | Panasonic | ERJ-3EKF75R0V | Volume Production | Newark | 65T8518 | 0.003 | 0.006
 | CRCW0603150RFKEA | RES Thick Film, 150Ω, 1%, 0.1W, 100ppm/°C, 0603 | R150_1 | CMP-2000-03913-2 | Up to date | Vishay | CRCW0603150RFKEA | Volume Production | Newark | 52K8161 | 0.005 | 0.005
 | SML-210MTT86 | LED GREEN CLEAR 0805 SMD | Status | CMP-08952-000013-1 | Up to date | Rohm | SML-210MTT86 | Not Recommended for New Design | Future Electronics | 9239369 | 0.34 | 1.36
 | B3U-1000P-B | SWITCH TACTILE SPST-NO 0.05A 12V | SW1 | CMP-08834-000005-1 | Up to date | Omron | B3U-1000P-B | Volume Production | Newark | 39M4616 | 0.66 | 0.66
 | STM32F722RET6 | IC MCU 32BIT 512KB FLASH 64LQFP | U1 | CMP-12105-000139-1 | Up to date | STMicroelectronics | STM32F722RET6 | Volume Production
 | MPU-6000 | 3-Axis Gyroscope 3-Axis Accelerometer Motion Processing Unit with I2C and SPI, 2.5, 3 or 3.3 V, -40 to 85 degC, 24-Pin QFN, RoHS, Tape and Reel | U2 | CMP-2000-05008-1 | Up to date | TDK InvenSense | MPU-6000 | Unknown
 | BMP280 | SENSOR PRESSURE ABS | U3 | CMP-2000-05076-3 | Up to date | Bosch | BMP280 | End of Life
 | TLV76790QWDRBRQ1 | IC OPAMP | U4 | CMP-04917-000367-1 | Up to date | Texas Instruments | TLV76790QWDRBRQ1 | Volume Production | Mouser | 595-TLV76790QWDRBRQ1 | 1.49 | 2.98
 | UA78L05CPK | IC REG LINEAR 5V 100MA SOT89-3 | U5 | CMP-2000-07341-2 | Up to date | Texas Instruments | UA78L05CPK | Volume Production | Digi-Key | 296-13531-1-ND | 0.49 | 0.49
 | LD1117S33TR | Fixed Low Drop Positive Voltage Regulator, 3.3V, 4-Pin SOT-223, Tape and Reel | U6 | CMP-0244-00310-1 | Up to date | STMicroelectronics | LD1117S33TR | Volume Production | Newark | 96AC0453 | 0.307 | 0.307
 | MAX7456EUI+T | IC DISPLAY 1CH W/EEPROM 28TSSOP | U8 | CMP-05676-000004-1 | Up to date | Maxim | MAX7456EUI+T | Obsolete
 | TLV76790QWDRBRQ1 | IC OPAMP | U9 | CMP-04917-000367-1 | Up to date | Texas Instruments | TLV76790QWDRBRQ1 | Volume Production | Mouser | 595-TLV76790QWDRBRQ1 | 1.49 | 2.98
 | CSTCE8M00G55-R0 | Ceramic Resonator, 8 MHz, +/- 0.5%, -20 to 80 degC, 3-Pin SMD, RoHS, Tape and Reel | X1 | CMP-2100-03620-1 | Up to date | Murata | CSTCE8M00G55-R0 | End of Life
 | ABM3-27.000MHZ-D2Y-T | Crystal 27MHz ±20ppm 18pF SMD-2 5mm x 3.2mm | Y2 | CMP-27762-013610-1 | Up to date | Abracon | ABM3-27.000MHZ-D2Y-T | Volume Production | Arrow Electronics | ABM3-27.000MHZ-D2Y-T | 0.4012 | 0.4012

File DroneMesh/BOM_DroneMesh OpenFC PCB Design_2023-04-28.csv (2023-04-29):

ID | Name | Designator | Footprint | Quantity | Manufacturer Part | Manufacturer | Supplier | Supplier Part | Price | Pins
1 | 0.1uf | C11_G,C13_G | 0805 | 2 |  |  |  |  |  | 2
2 | 2.2nf | C12_G | 0805 | 1 |  |  |  |  |  | 2
3 | USB_MICRO-B_FEMALE-SMT | J1 | USB-B-MICRO-SMD | 1 |  |  |  |  |  | 8
4 | NCP1117ST33T3G | U4 | SOT-223 | 1 |  |  |  |  |  | 4
5 | 10uf | C16_VREG,C17_VREG | 0805 | 2 |  |  |  |  |  | 2
6 | 100nf | C1,C2,C3,C4,C5,C6,C7 | 0805 | 7 |  |  |  |  |  | 2
7 | 22 | R3_USB,R6_USB | 0402 | 2 |  |  |  |  |  | 2
8 | 1k | R4_LED,R5_LED | 0402 | 2 |  |  |  |  |  | 2
9 | LED | LED1,LED2 | CHIPLED_0805 | 2 |  |  |  |  |  | 2
10 | BAT54C | D1 | SOT-23(SOT-23-3) | 1 |  |  |  |  |  | 3
11 | 1uf | C6_G | 0805 | 1 |  |  |  |  |  | 2
12 | 10k | R2_G,R1_BOOT,R8_USB,R1,R2,R3,R7 | 0402 | 7 |  |  |  |  |  | 2
13 | 8MHz | X1 | 3213 | 1 |  |  |  |  |  | 3
14 | DHT-4235A | SW2 | SW4-SMD-4.2X3.2X2.5MM | 1 |  |  |  |  |  | 4
15 | BC817W | Q1 | SOT-323(SC-70) | 1 |  |  |  |  |  | 3
16 | 4.7k | R4 | 0402 | 1 |  |  |  |  |  | 2
17 | STM32F405RGT6 | U1 | LQFP-64_10X10X05P | 1 |  |  |  |  |  | 64
18 | MPU-6000 | U3 | QFN-24 | 1 |  |  |  |  |  | 24

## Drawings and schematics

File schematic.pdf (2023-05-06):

Gyro / Accelerometer | LED's
(May need to eventually switch to BMI270 due to availability) | Barometer pretty straight forward connections 3.3V

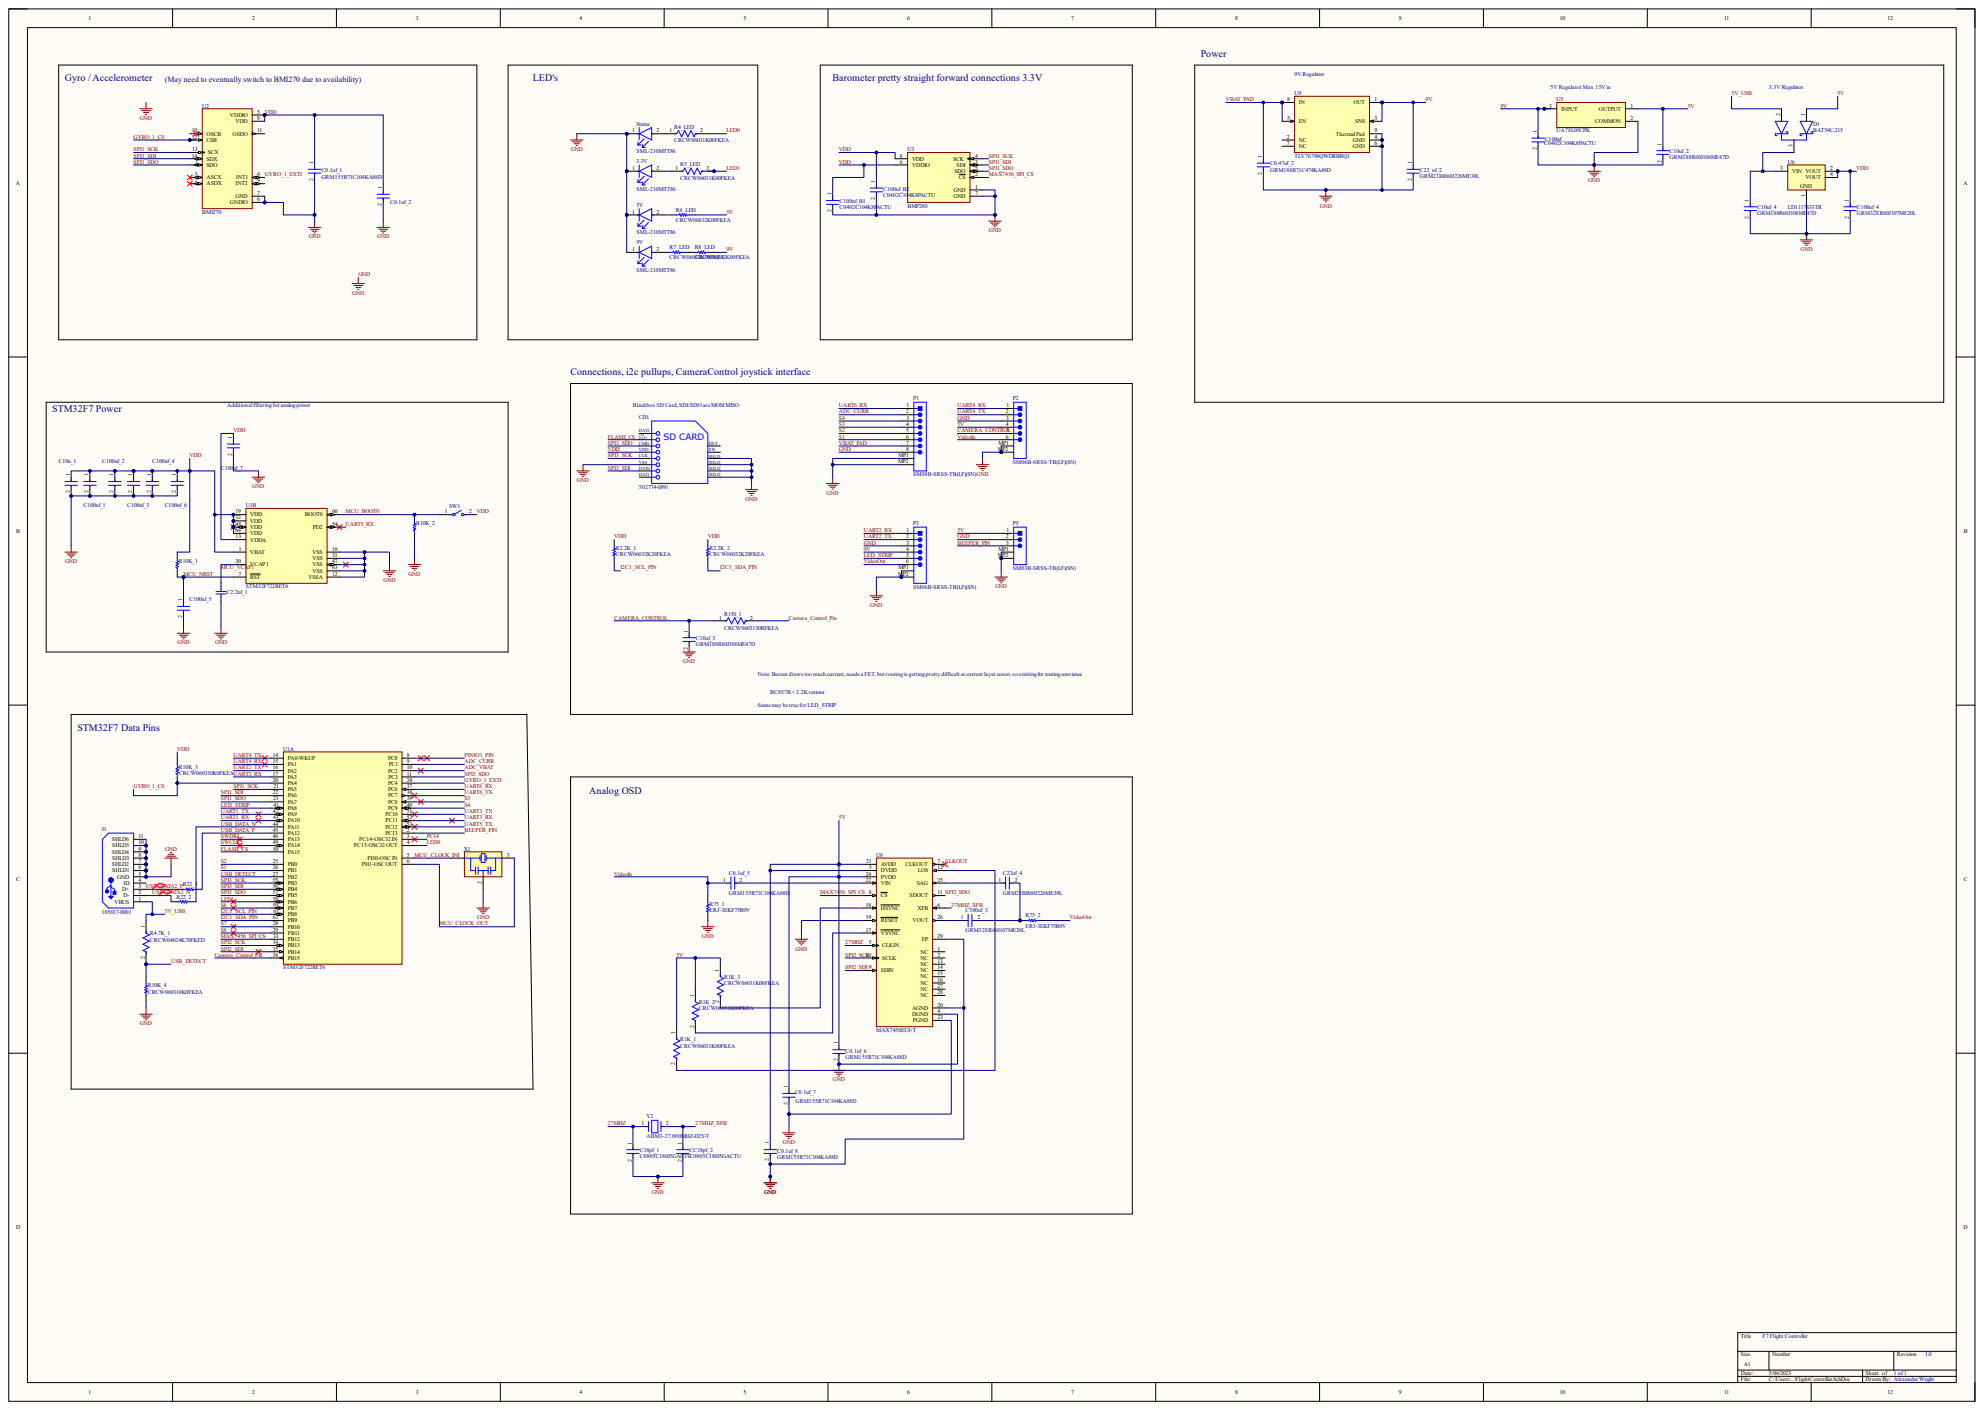
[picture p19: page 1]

Connections, i2c pullups, CameraControl joystick interface

Additional filtering for analog power
VDD 1 2

SM06B-SRSS-TB(LF)(SN)

SM08B-SRSS-TB(LF)(SN)

SM03B-SRSS-TB(LF)(SN)

Note: Buzzer draws too much current, needs a FET, but routing is getting pretty difficult at current layer count, so omiting for routing convience

Same may be true for LED_STRIP

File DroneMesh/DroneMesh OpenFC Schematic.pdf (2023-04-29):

# SBUS INVERTER UART1

# 5V_USB 3.3V REG

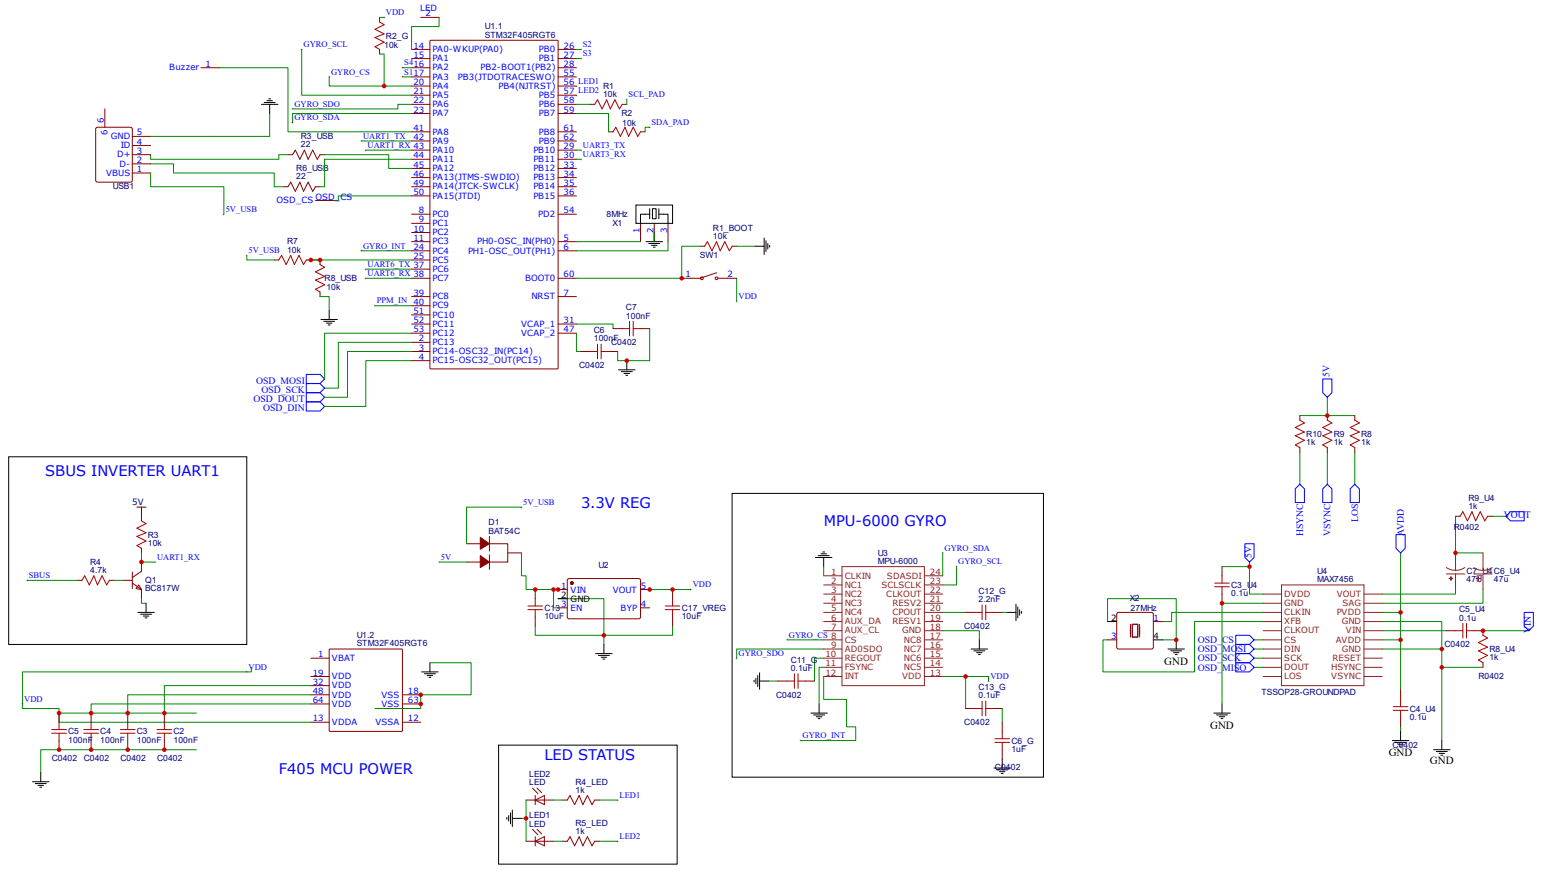
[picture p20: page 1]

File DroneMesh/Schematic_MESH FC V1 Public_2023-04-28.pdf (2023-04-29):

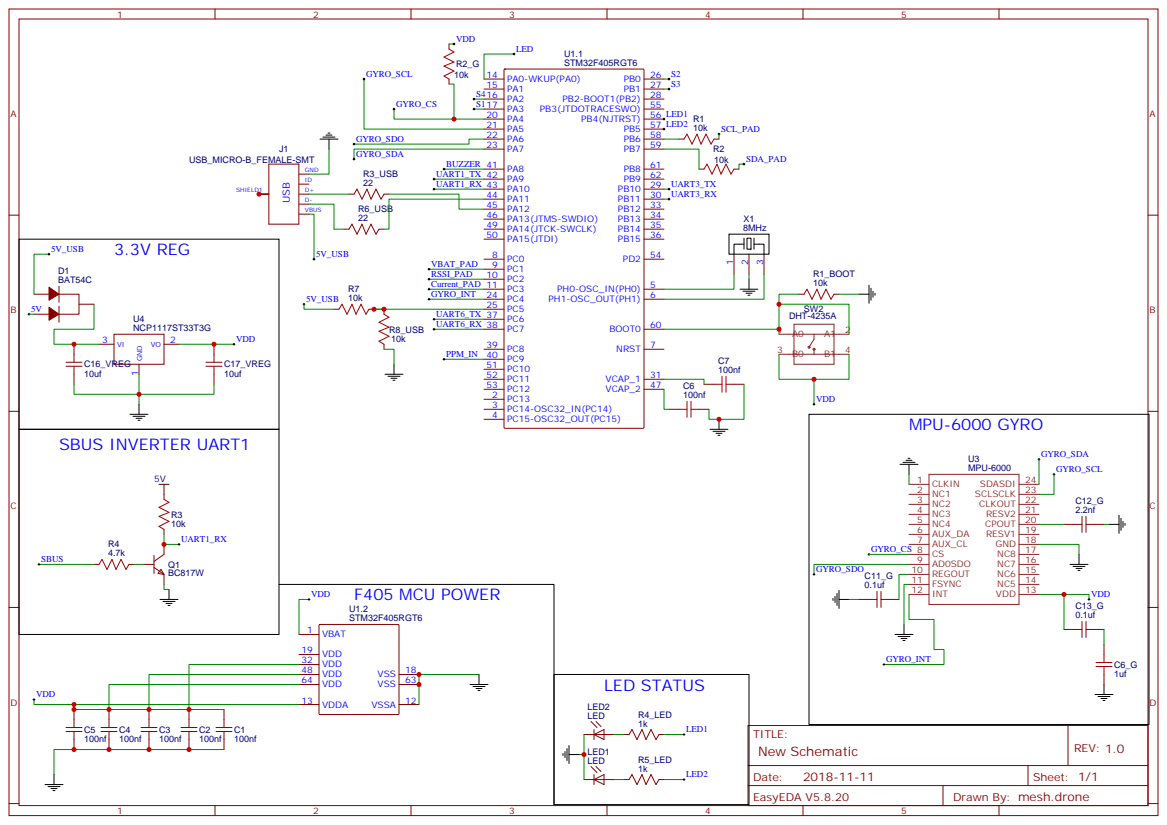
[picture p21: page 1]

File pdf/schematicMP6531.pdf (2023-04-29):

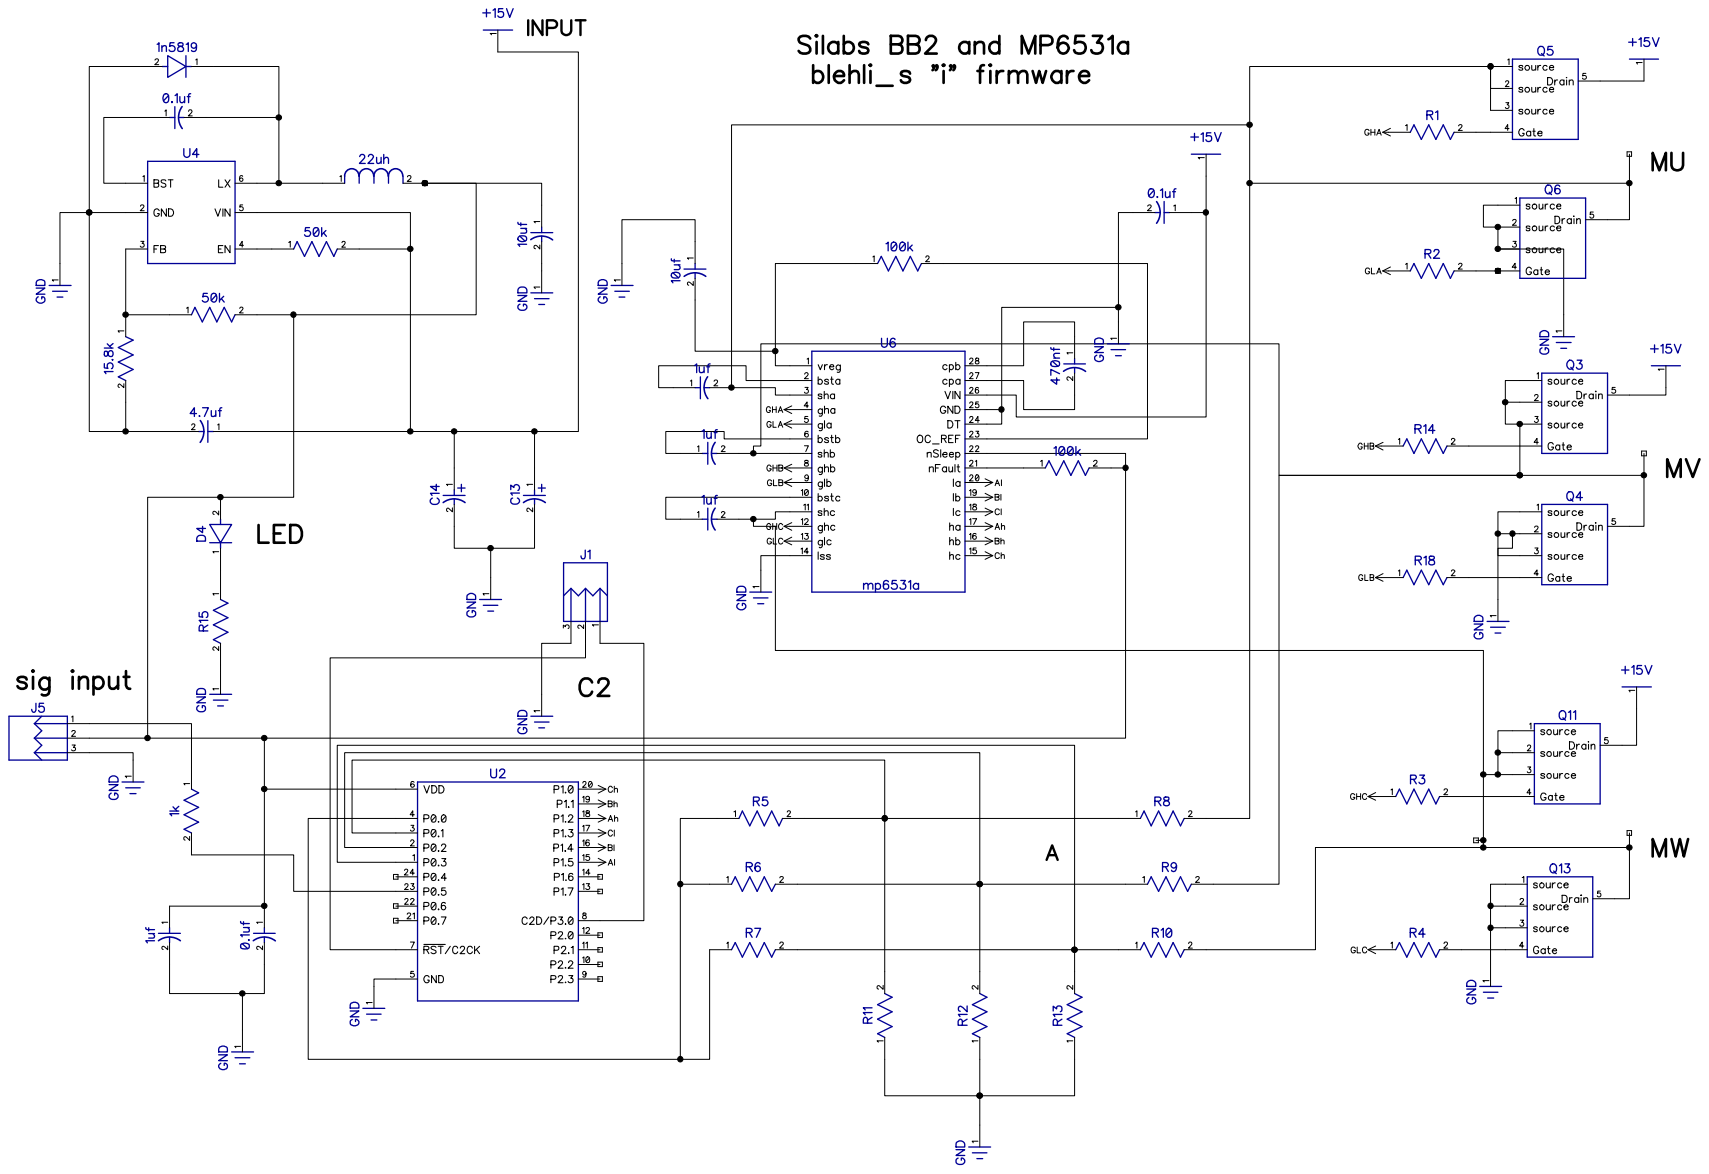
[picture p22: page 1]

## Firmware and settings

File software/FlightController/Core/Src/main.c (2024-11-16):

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
/* Includes ------------------------------------------------------------------*/
#include "main.h"
#include "fatfs.h"
#include "usb_device.h"

/* USER CODE BEGIN Includes */
#include "usbd_cdc_if.h"

#include <stdarg.h>
/* USER CODE END Includes */

ADC_HandleTypeDef hadc1;
ADC_HandleTypeDef hadc2;

I2C_HandleTypeDef hi2c1;

SPI_HandleTypeDef hspi1;
SPI_HandleTypeDef hspi2;
SPI_HandleTypeDef hspi3;

UART_HandleTypeDef huart4;
UART_HandleTypeDef huart5;
UART_HandleTypeDef huart1;
UART_HandleTypeDef huart2;
UART_HandleTypeDef huart3;
UART_HandleTypeDef huart6;

void SystemClock_Config(void);
static void MX_GPIO_Init(void);
static void MX_ADC1_Init(void);
static void MX_ADC2_Init(void);
static void MX_I2C1_Init(void);
static void MX_SPI1_Init(void);
static void MX_USART2_UART_Init(void);
static void MX_USART3_UART_Init(void);
static void MX_USART6_UART_Init(void);
static void MX_SPI2_Init(void);
static void MX_UART4_Init(void);
static void MX_UART5_Init(void);
static void MX_USART1_UART_Init(void);
static void MX_SPI3_Init(void);
/* USER CODE BEGIN 0 */

#include "bmp280.h"

void delay_ms(uint32_t period_ms);
int8_t i2c_reg_write(uint8_t i2c_addr, uint8_t reg_addr, uint8_t *reg_data, uint16_t length);
int8_t i2c_reg_read(uint8_t i2c_addr, uint8_t reg_addr, uint8_t *reg_data, uint16_t length);
int8_t spi_reg_write(uint8_t cs, uint8_t reg_addr, uint8_t *reg_data, uint16_t length);
int8_t spi_reg_read(uint8_t cs, uint8_t reg_addr, uint8_t *reg_data, uint16_t length);
void print_rslt(const char api_name[], int8_t rslt);


//static uint8_t BMP280_ADDR  = (0xF6);
static uint8_t BMP280_ID_REG  = (0x80 | 0xD0);
static uint8_t BMI270_ID_REG  = (0x80 | 0x00);


static const uint8_t TMP102_ADDR = 0x48 << 1;
static const uint8_t REG_TEMP = 0x0;




char spi_buf[32];

void usb_printf(const char *fmt, ...)
{
  static char buffer[256];
  va_list args;
  va_start(args, fmt);
  vsnprintf(buffer, sizeof(buffer), fmt, args);
  va_end(args);

  int len = strlen(buffer);

  CDC_Transmit_FS((uint8_t *)buffer, len);
}

// BMP280 is SPI1 in the schematic, but CubeIDE has pin33 marked as SPI2
// nope wrong, everything is SPI1, but they use SPI1_CS and SPI2_CS to select between BMP280 and BMI270
void SPI1_bmp280_read_id_register()
{
	char data[4] = {0};

	data[0] = BMP280_ID_REG;
	data[1] = BMP280_ID_REG;



  // Read ID register

	// Set chip select low
	HAL_GPIO_WritePin(SPI2_CS_GPIO_Port, SPI2_CS_Pin, GPIO_PIN_RESET);
	HAL_Delay(1);
	HAL_SPI_Transmit(&hspi1, (uint8_t *)&data[0], 1, 100);
	HAL_SPI_Receive(&hspi1, (uint8_t *)&spi_buf[0], 1, 100);
	HAL_Delay(1);
	HAL_GPIO_WritePin(SPI2_CS_GPIO_Port, SPI2_CS_Pin, GPIO_PIN_SET);

	// print out status register, should be 0x58
	usb_printf("BMP280 ID Reg: 0x%02X 0x%02X 0x%02X 0x%02X\r\n",
		  (unsigned int)spi_buf[0],
		  (unsigned int)spi_buf[1],
		  (unsigned int)spi_buf[2],
		  (unsigned int)spi_buf[3]);
}


static BYTE my_xchg_spi (
	BYTE dat	/* Data to send */
)
{
	BYTE rxDat;
    HAL_SPI_TransmitReceive(&hspi1, &dat, &rxDat, 1, 50);
    return rxDat;
}


void SPI1_bmp280_read_id_register_xchg()
{
	HAL_GPIO_WritePin(SPI2_CS_GPIO_Port, SPI2_CS_Pin, GPIO_PIN_RESET);
	HAL_Delay(1);
	spi_buf[0] = my_xchg_spi(0x80 | 0xD0);				/* Start + command index */
	spi_buf[0] = my_xchg_spi(0x80 | 0xD0);				/* Start + command index */
	HAL_Delay(1);
	HAL_GPIO_WritePin(SPI2_CS_GPIO_Port, SPI2_CS_Pin, GPIO_PIN_SET);

	usb_printf("BMP280 xchg Reg: 0x%02X 0x%02X 0x%02X 0x%02X\r\n",
		  (unsigned int)spi_buf[0],
		  (unsigned int)spi_buf[1],
		  (unsigned int)spi_buf[2],
		  (unsigned int)spi_buf[3]);

}

void SPI1_bmi270_read_id_register_xchg()
{
	HAL_GPIO_WritePin(SPI1_CS_GPIO_Port, SPI1_CS_Pin, GPIO_PIN_RESET);
	HAL_Delay(1);
	spi_buf[0] = my_xchg_spi(0x80 | 0x0);				/* Start + command index */
	spi_buf[0] = my_xchg_spi(0x80 | 0x0);				/* Start + command index */
	HAL_Delay(1);
	HAL_GPIO_WritePin(SPI1_CS_GPIO_Port, SPI1_CS_Pin, GPIO_PIN_SET);

	usb_printf("BMI270 xchg Reg: 0x%02X 0x%02X 0x%02X 0x%02X\r\n",
		  (unsigned int)spi_buf[0],
		  (unsigned int)spi_buf[1],
		  (unsigned int)spi_buf[2],
		  (unsigned int)spi_buf[3]);

}




// Note: have to do this twice as the first time it just enables the interface from i2c to spi
void SPI1_bmi270_read_id_register()
{
	char data[4] = {0};

	data[0] = BMI270_ID_REG; // dummy value
	data[1] = BMI270_ID_REG; // actual used value

// Read ID register

	// Set chip select low
	HAL_GPIO_WritePin(SPI1_CS_GPIO_Port, SPI1_CS_Pin, GPIO_PIN_RESET);
	HAL_Delay(1);
	HAL_SPI_Transmit(&hspi1, (uint8_t *)&data[0], 1, 100);
	HAL_SPI_Receive(&hspi1, (uint8_t *)&spi_buf[0], 1, 100);


//	HAL_StatusTypeDef ret = HAL_SPI_TransmitReceive(&hspi1, (uint8_t *)&data[0], (uint8_t *)&spi_buf[0], 2, 100);
//	if (ret != HAL_OK)
//	{
//		usb_printf("HAL_SPI_TransmitReceive failed %d\n", ret);
//	}
	HAL_Delay(1);
	HAL_GPIO_WritePin(SPI1_CS_GPIO_Port, SPI1_CS_Pin, GPIO_PIN_SET);
//	HAL_GPIO_WritePin(SPI2_CS_GPIO_Port, SPI2_CS_Pin, GPIO_PIN_SET);

	// print out status register, should be 0x24
	usb_printf("BMI270 ID Reg: 0x%02X 0x%02X 0x%02X 0x%02X\r\n",
		  (unsigned int)spi_buf[0],
		  (unsigned int)spi_buf[1],
		  (unsigned int)spi_buf[2],
		  (unsigned int)spi_buf[3]);
}



void SPI3_sdcard_read_id_register()
{
	char data[4] = {0};

	data[0] = BMI270_ID_REG; // dummy value
	data[1] = BMI270_ID_REG; // actual register

// Read ID register

	// Set chip select low
	HAL_GPIO_WritePin(SPI3_CS_GPIO_Port, SPI3_CS_Pin, GPIO_PIN_RESET);
	HAL_SPI_Transmit(&hspi3, (uint8_t *)&data[0], 2, HAL_MAX_DELAY);
	HAL_SPI_Receive(&hspi3, (uint8_t *)&spi_buf[0], 4, HAL_MAX_DELAY);
	HAL_GPIO_WritePin(SPI3_CS_GPIO_Port, SPI3_CS_Pin, GPIO_PIN_SET);


	// print out status register, should be 0x24
	usb_printf("SDCARD ID Reg: 0x%02X 0x%02X 0x%02X 0x%02X\r\n",
		  (unsigned int)spi_buf[0],
		  (unsigned int)spi_buf[1],
		  (unsigned int)spi_buf[2],
		  (unsigned int)spi_buf[3]);

}


// this is uses SPI1, but uses the MAX_Chip select, which is shared with SPI bus 2
void SPI2_max_analog_read_id_register()
{
//	char data[4] = {0};

//	data[0] = BMI270_ID_REG; // dummy
//	data[1] = BMI270_ID_REG; // actual register read

// Read ID register

	// Set chip select low
	// need to solder this chip on really
	/*
	HAL_GPIO_WritePin(SPI1_CS_GPIO_Port, SPI1_CS_Pin, GPIO_PIN_RESET);
	HAL_GPIO_WritePin(SPI2_CS_GPIO_Port, SPI2_CS_Pin, GPIO_PIN_RESET);
	HAL_SPI_Transmit(&hspi1, (uint8_t *)&data[0], 1, HAL_MAX_DELAY);
	HAL_SPI_Receive(&hspi1, (uint8_t *)&spi_buf[0], 4, HAL_MAX_DELAY);
	HAL_GPIO_WritePin(SPI1_CS_GPIO_Port, SPI1_CS_Pin, GPIO_PIN_SET);
	HAL_GPIO_WritePin(SPI2_CS_GPIO_Port, SPI2_CS_Pin, GPIO_PIN_SET);

	// print out status register, should be 0x24
	usb_printf("MAX Analog ID Reg: 0x%02X 0x%02X 0x%02X 0x%02X\r\n",
		  (unsigned int)spi_buf[0],
		  (unsigned int)spi_buf[1],
		  (unsigned int)spi_buf[2],
		  (unsigned int)spi_buf[3]);
		  */
}


int test_bmp280(void)
{
    int8_t rslt;
    struct bmp280_dev bmp;

    /* Map the delay function pointer with the function responsible for implementing the delay */
    bmp.delay_ms = delay_ms;

    bmp.dev_id = 0;
    bmp.read = spi_reg_read;
    bmp.write = spi_reg_write;
    bmp.intf = BMP280_SPI_INTF;
    rslt = bmp280_init(&bmp);
    print_rslt(" bmp280_init status", rslt);


    struct bmp280_uncomp_data data;

    bmp280_get_uncomp_data(&data, &bmp);

	usb_printf("BMP280 API : %u temp %u pressureX\r\n",
		  (unsigned int)data.uncomp_temp,
		  (unsigned int)data.uncomp_press);
    return 0;
}


void delay_ms(uint32_t period_ms)
{
	HAL_Delay(period_ms);
}


int8_t spi_reg_write(uint8_t cs, uint8_t reg_addr, uint8_t *reg_data, uint16_t length)
{
	HAL_GPIO_WritePin(SPI2_CS_GPIO_Port, SPI2_CS_Pin, GPIO_PIN_RESET);
	HAL_Delay(1);
	HAL_SPI_Transmit(&hspi1, (uint8_t *)&reg_addr, 1, 100);
	HAL_SPI_Transmit(&hspi1, (uint8_t *)reg_data, length, 100);
	HAL_Delay(1);
	HAL_GPIO_WritePin(SPI2_CS_GPIO_Port, SPI2_CS_Pin, GPIO_PIN_SET);

    return 0;
}


int8_t spi_reg_read(uint8_t cs, uint8_t reg_addr, uint8_t *reg_data, uint16_t length)
{
	HAL_GPIO_WritePin(SPI2_CS_GPIO_Port, SPI2_CS_Pin, GPIO_PIN_RESET);
	HAL_Delay(1);
	HAL_SPI_Transmit(&hspi1, (uint8_t *)&reg_addr, 1, 100);
	HAL_SPI_Receive(&hspi1, (uint8_t *)reg_data, length, 100);
	HAL_Delay(1);
	HAL_GPIO_WritePin(SPI2_CS_GPIO_Port, SPI2_CS_Pin, GPIO_PIN_SET);
    return 0;
}


void print_rslt(const char api_name[], int8_t rslt)
{
    if (rslt != BMP280_OK)
    {
    	usb_printf("%s\t", api_name);
        if (rslt == BMP280_E_NULL_PTR)
        {
        	usb_printf("Error [%d] : Null pointer error\r\n", (int)rslt);
        }
        else if (rslt == BMP280_E_COMM_FAIL)
        {
        	usb_printf("Error [%d] : Bus communication failed\r\n", (int)rslt);
        }
        else if (rslt == BMP280_E_IMPLAUS_TEMP)
        {
        	usb_printf("Error [%d] : Invalid Temperature\r\n", (int)rslt);
        }
        else if (rslt == BMP280_E_DEV_NOT_FOUND)
        {
        	usb_printf("Error [%d] : Device not found\r\n", (int)rslt);
        }
        else
        {
            /* For more error codes refer "*_defs.h" */
        	usb_printf("Error [%d] : Unknown error code\r\n", (int)rslt);
        }
    }
}



void read_tmp102()
{
	HAL_StatusTypeDef ret;
	char buf[32];
	int16_t val;
	float temp_c;

	strcpy(buf, "Hello!\r\n");
	HAL_UART_Transmit(&huart2, (uint8_t *)buf, strlen(buf), HAL_MAX_DELAY);


	buf[0] = REG_TEMP;
	ret = HAL_I2C_Master_Transmit(&hi2c1, TMP102_ADDR, (uint8_t *)buf, 1, HAL_MAX_DELAY);
	if ( ret != HAL_OK)
	{
		strcpy(buf, "i2c tx error\r\n");
	}
	else
	{
		ret = HAL_I2C_Master_Receive(&hi2c1, TMP102_ADDR, (uint8_t *)buf, 2, HAL_MAX_DELAY);
		if ( ret != HAL_OK)
		{
			strcpy(buf, "i2c rx error\r\n");
		}

		val = ( (int16_t)buf[0] << 4 | (buf[1] >> 4) );
		if (val > 0x7FF )
		{
			val |= 0xF000;
		}

		temp_c = val * 0.0625;
		temp_c *= 100;

		sprintf(buf, "%u.%02u C\r\n",
			((unsigned int)temp_c / 100),
			((unsigned int)temp_c % 100));
	}

	HAL_UART_Transmit(&huart2, (uint8_t *)buf, strlen(buf), HAL_MAX_DELAY);
}








// https://01001000.xyz/2020-08-09-Tutorial-STM32CubeIDE-SD-card/
void test_sdcard()
{
	  HAL_Delay(1000); //a short delay is important to let the SD card settle

	  FATFS FatFs; 	//Fatfs handle
	  FIL fil; 		//File handle
	  FRESULT fres; //Result after operations

	  //Open the file system
	  fres = f_mount(&FatFs, "", 1); //1=mount now

	  if (fres != FR_OK)
	  {
		  usb_printf("f_mount error (%i)\r\n", fres);
		  return;
	  }

	  //Let's get some statistics from the SD card
	  DWORD free_clusters, free_sectors, total_sectors;

	  FATFS* getFreeFs;

	  fres = f_getfree("", &free_clusters, &getFreeFs);
	  if (fres != FR_OK)
	  {
		  usb_printf("f_getfree error (%i)\r\n", fres);
		  return;
	  }

	  //Formula comes from ChaN's documentation
	  total_sectors = (getFreeFs->n_fatent - 2) * getFreeFs->csize;
	  free_sectors = free_clusters * getFreeFs->csize;

	  usb_printf("SD card stats:\r\n%10lu KiB total drive space.\r\n%10lu KiB available.\r\n", total_sectors / 2, free_sectors / 2);

	  //Now let's try to open file "test.txt"
	  fres = f_open(&fil, "test.txt", FA_READ);

	  if (fres != FR_OK)
	  {
		usb_printf("f_open error (%i)\r\n");
		return;
	  }

	  usb_printf("I was able to open 'test.txt' for reading!\r\n");

	  //Read 30 bytes from "test.txt" on the SD card
	  BYTE readBuf[30] = {0};

	  //We can either use f_read OR f_gets to get data out of files
	  //f_gets is a wrapper on f_read that does some string formatting for us
	  TCHAR* rres = f_gets((TCHAR*)readBuf, 30, &fil);

	  if(rres != 0)
	  {
		  usb_printf("Read string from 'test.txt' contents: %s\r\n", readBuf);
	  }
	  else
	  {
		  usb_printf("f_gets error (%i)\r\n", fres);
	  }

	  //Be a tidy kiwi - don't forget to close your file!
	  f_close(&fil);

	  //Now let's try and write a file "write.txt"
	  fres = f_open(&fil, "write.txt", FA_WRITE | FA_OPEN_ALWAYS | FA_CREATE_ALWAYS);

	  if(fres == FR_OK)
	  {
		  usb_printf("I was able to open 'write.txt' for writing\r\n");
	  }
	  else
	  {
		  usb_printf("f_open error (%i)\r\n", fres);
	  }

	  //Copy in a string
	  strncpy((char*)readBuf, "a new file is made!", 20);
	  UINT bytesWrote;
	  fres = f_write(&fil, readBuf, 19, &bytesWrote);

	  if(fres == FR_OK)
	  {
		  usb_printf("Wrote %i bytes to 'write.txt'!\r\n", bytesWrote);
	  }
	  else
	  {
		  usb_printf("f_write error (%i)\r\n");
	  }

	  //Be a tidy kiwi - don't forget to close your file!
	  f_close(&fil);

	  //We're done, so de-mount the drive
	  f_mount(NULL, "", 0);
}


int test_enable = 0;


#define	MCU_IRQS	70u

void start_bootloader()
{
	void (*boot_jump)(void);

	boot_jump = (void (*)(void))(*((uint32_t *)(0x1FFF0000 + 4)));

	HAL_RCC_DeInit();
	SysTick->CTRL = 0;
	SysTick->LOAD = 0;
	SysTick->VAL = 0;
	__disable_irq();
	SYSCFG->MEMRMP = 0x01;

	__set_MSP(*(uint32_t *)0x1FFF0000);

	boot_jump();

/*

	void (*boot_jump)(void);

	boot_jump = (void (*)(void))(*((uint32_t *)(0x1FFF0000 + 4)));

	HAL_DeInit();
	__set_MSP(*(__IO uint32_t*)0x1FFF0000);

	__disable_irq();

	SysTick->CTRL = 0;

	HAL_RCC_DeInit();
	for (uint8_t i = 0; i < (MCU_IRQS + 31u) / 32; i++)
	{
		NVIC->ICER[i]=0xFFFFFFFF;
		NVIC->ICPR[i]=0xFFFFFFFF;
	}

	__enable_irq();

	*((unsigned long *)0x2004FFF0) = 0xDEADBEEF; // 320KB STM32F7xx
	__DSB();

	boot_jump();
	*/
}


/* USER CODE END 0 */

/**
  * @brief  The application entry point.
  * @retval int
  */
int main(void)
{
  /* MCU Configuration--------------------------------------------------------*/

  /* Reset of all peripherals, Initializes the Flash interface and the Systick. */
  HAL_Init();

  /* Configure the system clock */
  SystemClock_Config();

  /* Initialize all configured peripherals */
  MX_GPIO_Init();
  MX_USB_DEVICE_Init();
  MX_ADC1_Init();
  MX_ADC2_Init();
  MX_I2C1_Init();
  MX_SPI1_Init();
  MX_USART2_UART_Init();
  MX_USART3_UART_Init();
  MX_USART6_UART_Init();
  MX_SPI2_Init();
  MX_UART4_Init();
  MX_UART5_Init();
  MX_USART1_UART_Init();
  MX_SPI3_Init();
  MX_FATFS_Init();
  /* USER CODE BEGIN 2 */

  __enable_irq();


  HAL_GPIO_TogglePin (LED1_GPIO_Port, LED1_Pin);



  // CS pin should be default high
	HAL_GPIO_WritePin(SPI1_CS_GPIO_Port, SPI1_CS_Pin, GPIO_PIN_SET);
	HAL_GPIO_WritePin(SPI2_CS_GPIO_Port, SPI2_CS_Pin, GPIO_PIN_SET);
	HAL_GPIO_WritePin(SPI3_CS_GPIO_Port, SPI3_CS_Pin, GPIO_PIN_SET);


  // Print something (probably will be too fast to connect and see?)
  usb_printf("STM32F7 main()\r\n");


//  SPI1_bmi270_read_id_register();

  test_bmp280();

  SPI1_bmp280_read_id_register();

  SPI1_bmi270_read_id_register();

  /* USER CODE END 2 */

  /* Infinite loop */
  /* USER CODE BEGIN WHILE */
  while (1)
  {
  	  if (test_enable)
	  {






		  if (test_enable == '`')
		  {
			  start_bootloader();
		  }

		  if (test_enable == '1')
		  {
			  test_sdcard();
		  }

		  if (test_enable == '2')
		  {
			  SPI1_bmp280_read_id_register();
		  }

		  if (test_enable == '3')
		  {
			  SPI1_bmi270_read_id_register();
		  }

		  if (test_enable == '4')
		  {
			  SPI1_bmi270_read_id_register_xchg();
		  }

		  if (test_enable == '5')
		  {
			  test_bmp280();
		  }

		  if (test_enable == '6')
		  {
			  SPI1_bmp280_read_id_register_xchg();
		  }

		  if (test_enable == '7')
		  {
			  static int init = 0;

			  if (init == 0)
			  {

//				  TMP117_Initialization(hi2c1);

				  uint16_t id = -1;

//				  id = TMP117_get_ID_Register(hi2c1);

			      static uint8_t sbuf[3] = { 0 };
			      static uint8_t rbuf[3] = { 0 };
			      sbuf[0] = 0x0F;

			      uint16_t addr = 0x48<<1;


			      HAL_I2C_Master_Transmit(&hi2c1, addr, sbuf, 1, HAL_MAX_DELAY);
			      HAL_Delay(1);
			      HAL_I2C_Master_Receive(&hi2c1, addr, rbuf, 2, HAL_MAX_DELAY);
			      id = ((rbuf[0]<<8)|rbuf[1]);



				  if (id == 0x0117)
				  {
					  usb_printf("tmp117 init pass\r\n");
					  init = 1;

				  }
				  else
				  {
					  usb_printf("tmp117 init fail returned %X [%X, %X]\r\n", (int)id, rbuf[0], rbuf[1]);
				  }


			  }

		      static uint8_t sbuf[3] = {0};
		      static uint8_t rbuf[3] = {0};
		      uint16_t addr = 0x48<<1;

		      sbuf[0] = 0x0;

		      HAL_I2C_Master_Transmit(&hi2c1, addr, sbuf, 1, HAL_MAX_DELAY);
		      HAL_Delay(1);
		      HAL_I2C_Master_Receive(&hi2c1, addr, rbuf, 2, HAL_MAX_DELAY);

		      float temp =  ( (rbuf[0] << 8) | rbuf[1] ) * 0.0078125;

		      int top = temp;

		      usb_printf("Tmp117 Temp %d [%X, %X]\r\n", top, rbuf[0], rbuf[1]);

		  }




		  test_enable = 0;
	  }


	  // blink leds
	  HAL_GPIO_TogglePin (LED0_GPIO_Port, LED0_Pin);
	  HAL_Delay (100);   /* Insert delay 100 ms */
	  HAL_GPIO_TogglePin (LED1_GPIO_Port, LED1_Pin);
	  HAL_Delay (100);   /* Insert delay 100 ms */
  
    /* USER CODE END WHILE */

    /* USER CODE BEGIN 3 */
  }
  /* USER CODE END 3 */
}

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


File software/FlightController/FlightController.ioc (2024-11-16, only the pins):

Mcu.UserName=STM32F722RETx
PA0-WKUP.Signal=UART4_TX
PA1.Signal=UART4_RX
PA10.Signal=USART1_RX
PA11.Signal=USB_OTG_FS_DM
PA12.Signal=USB_OTG_FS_DP
PA13.Signal=SYS_JTMS-SWDIO
PA14.Signal=SYS_JTCK-SWCLK
PA15.Signal=GPIO_Output
PA2.Signal=USART2_TX
PA3.Signal=USART2_RX
PA4.GPIO_Label=SPI1_CS
PA4.Signal=GPIO_Output
PA5.Signal=SPI1_SCK
PA6.Signal=SPI1_MISO
PA7.Signal=SPI1_MOSI
PA8.Signal=GPIO_Output
PA9.Signal=USART1_TX
PB0.Signal=GPIO_Output
PB1.Signal=GPIO_Output
PB10.Signal=GPIO_Output
PB11.Signal=GPIO_Output
PB12.GPIO_Label=SPI2_CS
PB12.Signal=GPIO_Output
PB13.Signal=SPI2_SCK
PB14.Signal=SPI2_MISO
PB15.Signal=GPIO_Output
PB3.Signal=SPI3_SCK
PB4.Signal=SPI3_MISO
PB5.Signal=SPI3_MOSI
PB6.GPIO_Label=LED1
PB6.Signal=GPIO_Output
PB7.GPIO_Label=SPI3_CS
PB7.Signal=GPIO_Output
PB8.Signal=I2C1_SCL
PB9.Signal=I2C1_SDA
PC0.Signal=GPIO_Output
PC1.Signal=ADCx_IN11
PC10.Signal=USART3_TX
PC11.Signal=USART3_RX
PC12.Signal=UART5_TX
PC13.Signal=GPIO_Output
PC14-OSC32_IN.Signal=GPXTI14
PC15-OSC32_OUT.GPIO_Label=LED0
PC15-OSC32_OUT.Signal=GPIO_Output
PC2.Signal=ADCx_IN12
PC3.Signal=SPI2_MOSI
PC4.Signal=GPXTI4
PC6.Signal=USART6_TX
PC7.Signal=USART6_RX
PC8.Signal=GPIO_Output
PC9.Signal=GPIO_Output
PD2.Signal=UART5_RX
PH0-OSC_IN.Signal=RCC_OSC_IN
PH1-OSC_OUT.Signal=RCC_OSC_OUT

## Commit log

2023-04-29 add some files
    [BOM_DroneMesh OpenFC PCB Design_2023-04-28.csv, FlightController.SchDoc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]
2023-04-29 This schematic has the OSD chip, not sure if it works
2023-04-29 add BOM and work in progress PCB layout, update schematic
    [FlightController.PrjPcb, FlightController.SchDoc, PCB1.PcbDoc]
2023-04-29 move to project directory, resize board, add pads
    [FlightController.PrjPcb, FlightController.SchDoc, PCB1.PcbDoc]
2023-04-29 add some screen shots of pcb 3d view
2023-04-29 attempt to fix validation errors
    [FlightController.SchDoc, PCB1.PcbDoc]
2023-04-30 had to revert a lot as I lost my pads for some reason, rotate leds attempt routing
    [FlightController.SchDoc, PCB1.PcbDoc]
2023-04-30 add named / footprinted caps and resistors
    [FlightController.SchDoc]
2023-04-30 place capacitors and resistors whereever they fit
    [FlightController.PrjPcb, FlightController.SchDoc, PCB1.PcbDoc]
2023-04-30 shrink fonts mainly
    [PCB1.PcbDoc]
2023-04-30 autorouter not doing so great 84.23% routed
    [FlightController.PrjPcb, FlightController.SchDoc, PCB1.PcbDoc]
2023-04-30 update schematic
2023-04-30 Move resistors / caps closer to where they are used
    [FlightController.SchDoc, PCB1.PcbDoc]
2023-04-30 rework MAX7456 from datasheet
    [FlightController.SchDoc, PCB1.PcbDoc]
2023-04-30 Add some connectors, resync pin assignment to match JBF7V2
    [FlightController.SchDoc, PCB1.PcbDoc]
2023-04-30 update pcb images
2023-04-30 Follow datasheet for BMP280 (add some caps)
    [FlightController.SchDoc, PCB1.PcbDoc]
2023-04-30 Commit before autoroute attempt
    [PCB1.PcbDoc]
2023-04-30 Routing finished, no constraints, but not everything routed
    [PCB1.PcbDoc]
2023-05-01 Add switched 9v, switch regulators to smaller ones
    [FlightController.SchDoc, PCB1.PcbDoc]
2023-05-01 minor changes
    [FlightController.SchDoc, PCB1.PcbDoc]
2023-05-01 Add USB detect voltage divider
    [FlightController.SchDoc]
2023-05-01 remove some pads and move connectors back a bit
2023-05-01 Fix some schematic validation warnings (wrong net names in places)
    [FlightController.SchDoc]
2023-05-01 Add gerber files (I wouldn't make just yet)
    [FlightController.PrjPcb, FlightController.SchDoc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]
2023-05-02 Rework board layers, top, bottom, vdd, ground, two additional signals
    [FlightController.SchDoc, PCB1.PcbDoc]
2023-05-02 update gerbers
    [PCB1.GBL, PCB1.GBO, PCB1.GBP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]
2023-05-02 Misc fixes, all routed, but one contention?
    [FlightController.SchDoc, PCB1.PcbDoc]
2023-05-02 update schematic and images
2023-05-02 Commit current state, 11 contentions all routed
    [FlightController.SchDoc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]
2023-05-02 add BOM xlsx
    [FlightController.xlsx]
2023-05-02 add BOM csv
    [BOM_FlightController.csv]
2023-05-03 Manual route layer one (need vias now)
    [FlightController.SchDoc, PCB1.PcbDoc]
2023-05-03 Re-add mounting holes and resize PCB
    [PCB1.PcbDoc]
2023-05-03 Address some design rules settings / violations
    [FlightController.SchDoc, PCB1.PcbDoc]
2023-05-03 minor reshuffling of caps
    [FlightController.SchDoc, PCB1.PcbDoc]
2023-05-03 Add some vias
    [PCB1.PcbDoc]
2023-05-03 Lots of manual routing and vias
    [FlightController.SchDoc, PCB1.PcbDoc]
2023-05-03 All nets routed
    [FlightController.SchDoc, PCB1.PcbDoc]
2023-05-03 Bring out i2c pins to bottom
    [FlightController.SchDoc, PCB1.PcbDoc]
2023-05-03 Fix minor design rule problems that got introduced somehow, update gerbers again
    [PCB1.GBL, PCB1.GBO, PCB1.GBP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]
2023-05-03 Add pick and place file
    [FlightController.PrjPcb]
2023-05-04 Set some design rules, larger via spacing, larger min tracks
    [FlightController.PrjPcb, PCB1.PcbDoc, Pick Place for PCB1.csv]
2023-05-04 Slightly larger design rules for manufacturability
    [PCB1.PcbDoc]
2023-05-04 Just sync everything
    [Bill of Materials-FlightController.xls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]
2023-05-04 Regenerate gerbers (hopefully with drill files this time)
    [Bill of Materials-FlightController.xls, FlightController.SchDoc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]
2023-05-04 Sync before closing altium
    [Bill of Materials-FlightController.xls, Copy of Bill of Materials-FlightController.xlsx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]
2023-05-04 Make routes less curvy
    [PCB1.PcbDoc]
2023-05-04 Fix ground power planes
    [PCB1.PcbDoc]
2023-05-04 Ground / Power Planes weren't saving gerbers... fixed
    [Bill of Materials-FlightController.xls, Copy of Bill of Materials-FlightController.xlsx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]
2023-05-05 Just sync and tag for now, will likely need to make part swaps based on part availability as a lot of stuff is out of stock
    [FlightController.SchDoc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]
2023-05-05 update schematic to v0.2
2023-05-05 add assembly drawings
2023-05-05 add PCBDwf file, sync others
    [FlightController.PrjPcb, PCB1.PcbDoc]
2023-05-05 Minor update, correct tag connect pinout and move usb connector up some
    [PCB1.PcbDoc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]
2023-05-05 remove some extraneous traces after moving usb connector up
    [Bill of Materials-FlightController.xls, Copy of Bill of Materials-FlightController.xlsx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]
2023-05-06 Think this version may actually get made, time will tell
    [Copy of Bill of Materials-FlightController.xlsx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]
2023-05-06 Add load caps to the 27mhz crystal
    [Bill of Materials-FlightController.xls, Copy of Bill of Materials-FlightController.xlsx, FlightController.SchDoc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]
2023-05-06 Switch MPU6000 to BMI270
    [FlightController.SchDoc, PCB1.PcbDoc]
2023-05-06 Fix some unrouted nets that snuck up
    [FlightController.SchDoc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]
2023-05-06 Just commit just in case
    [PCB1.PcbDoc]
2023-05-06 sync bom doc cause it wasnt for some reason
2023-05-06 update schematic to what JLCPCB is making
2023-05-15 add first board spin images
2023-05-16 add images with missing caps / resistors marked
2023-07-26 Too busy to solder, attempt 1 has a LED going at least, think there might be a short in my soldering. The 0402 capacitors are a pain, but 0603 size isn't bad, might redesign to use no smaller than 06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
2023-07-26 Slight clearance issue around sdcard slot, but grommets fit and holes seem to be spaced correctly
2023-08-05 Board2 soldered, DFU mode works! Now to blink LEDs
2023-08-05 Blinking LED0 and LED1! Need to check peripherals
2023-12-09 echo upper case on USB com port
2023-12-09 add some spi code, no valid responses yet
2023-12-09 misc prototype code
2023-12-10 SPI read/write to sdcard works (surprised that's the first one tbh)
2023-12-21 update rev1 text, sadly need a board spin for SPI
2023-12-28 i2c works with TMP117 sensor
2023-12-28 add pad photos + i2c setup
2024-11-16 update on the SPI flipping
2024-12-25 add solder pen update

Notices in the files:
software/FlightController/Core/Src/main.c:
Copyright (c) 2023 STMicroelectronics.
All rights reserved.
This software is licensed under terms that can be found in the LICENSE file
